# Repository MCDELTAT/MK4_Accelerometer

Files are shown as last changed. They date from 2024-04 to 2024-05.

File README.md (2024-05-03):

## Prusa MK4 Accelerometer

If you're reading this it's likely because you've [noticed][3] that your MK4 xBuddy Controller has a port reserved for an accelerometer and wondered "Hmmm. I wonder if that works."

I'm happy to report that the answer is "Yes." I found it to be reliable and working just fine, but in response to my demo, Josef Prusa himself responded "Hi! Please note the code is not tested on MK4 so you shouldn't count on it's results. There will be an official implementation but not ETA yet." Source [here][4].

This repository contains information, designs, and tools for using an accelerometer with the Prusa MK4 3D Printer.

This primary document is focused on being a quick start guide, while other documents in the repository contain more in-depth technical information about other aspects of the project.

## Future Work
Here's a roadmap of a few simple tasks that I'd like to accomplish with this project.

- [x] Design mounts for the Toolhead and Bed that work with both custom and off the shelf boards.
- [x] Test other chips like the LIS3DH for compatibility.
- [ ] Run print tests and document outcomes (IN PROGRESS)
- [ ] Design our own custom PCB with a compatible Molex Clik-MATE connector (IN PROGRESS-Design Complete, Validation Underway)
    * This will allow users to install an accelerometer quickly and without all the tools needed to solder.

## Compatability
* At the moment, only MCDELTAT has confirmed the accelerometer as working on firmware versions 5.2.1 and 6.0.0. Their printer uses the 2021 0.2.7 xBuddy board. Two other community members have tried on printers that use the 0.3.7 board and are not seeing similar signals on their ports. I'm working with them and hoping Prusa will release the older schematics so I can compare.

## ⚠️ HALT - Warranty Check
Q: Does this void my warranty?

A: Probably.

You can read the official Prusa Warranty on their website [here][1]. Quote "This warranty is **voided by:** ... Upgrades or add-ons that are not officially supported."

This modification does not require you to compile or upload any custom firmware to work. The release firmware directly from Prusa supports these boards, so this is purely a hardware addition. That said, I will include thorough warnings where appropriate to ensure that nothing goes wrong, should you follow the instructions correctly.

## Tools and Part Requirements
Here is a list of tools that will be needed to add an accelerometer board at the moment.
1. Clik-MATE 6 Pin Cable Assembly (MPN: 0151350606 for 600mm). Digikey [source][2]
2. LIS2DH Accelerometer board ready for SPI communication.
    * See the table below for a table of boards that have been tested and verified as working.
3. Soldering Iron and related tools.
4. (Optional) A multimeter will be helpful.
5. Mounts for the board. 3D Printable mounts for the X and Y-Axis can be found [here][9]. The mounts are designed for MK4 printers, but the mounting tray is designed to be modular. At the moment the only tray is for the generic accelerometer boards. I will provide another tray for my custom board later.
6. Some kind of computer capable of controlling your MK4 Printer and a USB-C Cable. I tested everything with a Raspberry Pi running Octoprint, but any compatible software should be functional. For example, Mainsail or Pronterface should be more than capable.

## Soldering Your Accelerometer Board
For this section, I will document the soldering procedure for the generic purple Chinese LIS2DH boards, as that is the first board I confirmed to be working.

1. Power off your printer. Unplug it from it's power source. 
2. (Optional but recommended). Insert one end of your cable assembly into the Accelerometer port of the board. The connector is keyed and will only fit one direction, with the release arm facing towards the center of the board (back of the printer). Pull it back out and use a marker to color the top side of the connector. This will help you to keep track of which pin belongs to each cable.
3. Cut the cable assembly with a wire stripper or other tool. Goodbye beautiful connector.
4. Strip off approximately 5mm of the outer wire insulator for each cable.
5. (Optional tinning technique). Heat up your soldering iron, twist the stranded wires of a single cable together tightly, and apply solder to the wires. This makes it into one solid connector and makes it easier to solder to the accelerometer board later.
6. Identify the first wire to solder. If you did step two, the top side that you marked is pin 6 on the Prusa Schematics and Connector documentation. (See the Diagram below). On the Digikey cable assembly, they use tape in the middle of the cables to group them to together. We have two options:

    a) Cut the tape and visually trace the cables.

    b) Leave the tape intact and use a multimeter to buzz out which cable is connected to each connector pin. This can be done by switching to continuity mode, touching one lead to a cable of your choice, and the other to small pad on the back of the connector.
7. Solder the wire to the correct position. Repeat steps 5 and 6, finding the correct wires and soldering them to the board. A table is provided below for reference.
8. Snip the extra wire that wasn't covered by the solder joint.

## Pinout
Here is a reference table for the Prusa Connector Pins and the breakout board. Prusa's documentation supporting this is found [here][5].

| Connector | Pin (Prusa) | Pin (Accel Board) | Type | Function | GPIO | Limitations  |
|---|---|---|---|---|---|---|
| J29 (ACCELEROMETER) | 1 | CS | open drain output | SPI2 CS  | PA10 | Max 3.3V/5mA |
| J29 (ACCELEROMETER) | 2 | SCL | input/output | SPI2 SCL | PB10 | Max 5V/5mA |
| J29 (ACCELEROMETER) | 3 | SDA | input/output | SPI2 SDI | PC3  | Max 5V/5mA |
| J29 (ACCELEROMETER) | 4 | SDO | input/output | SPI2 SDO | PC2  | Max 5V/5mA |
| J29 (ACCELEROMETER) | 5 | VCC | 3V3 | Power | x | Max 50mA |
| J29 (ACCELEROMETER) | 6 | GND | GND | Power | x | x |

## Pinout Images
### Connector Side:
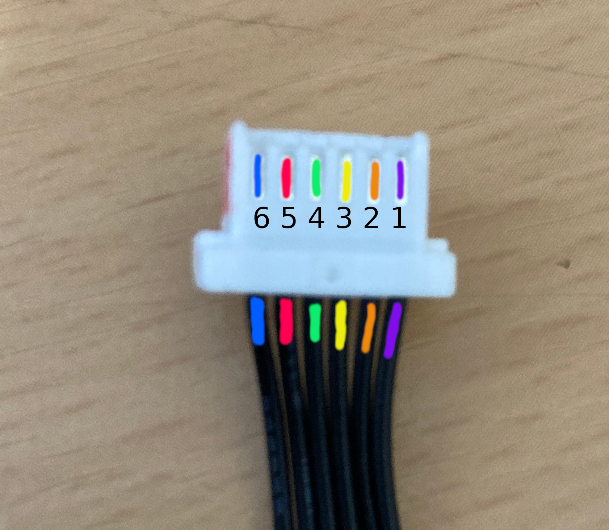
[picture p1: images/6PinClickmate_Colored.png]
ClickMate Male Connector Colored Pinout


### Adafruit Board:
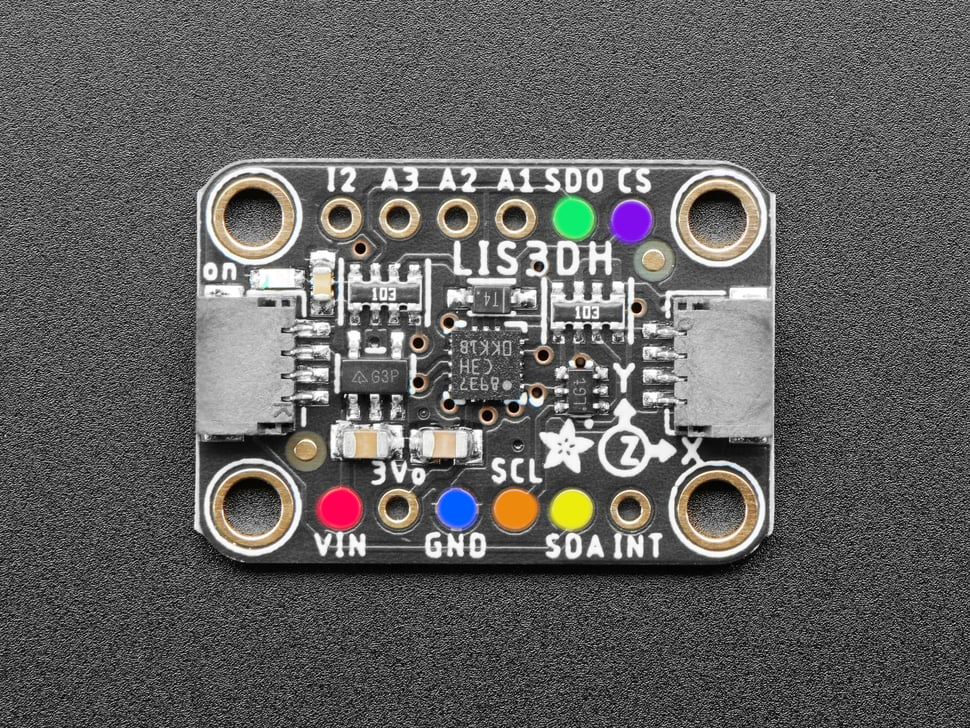
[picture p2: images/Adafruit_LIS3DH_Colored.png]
Adafruit LIS3DH Board Colored Pinout


### Generic LIS2DH Board:
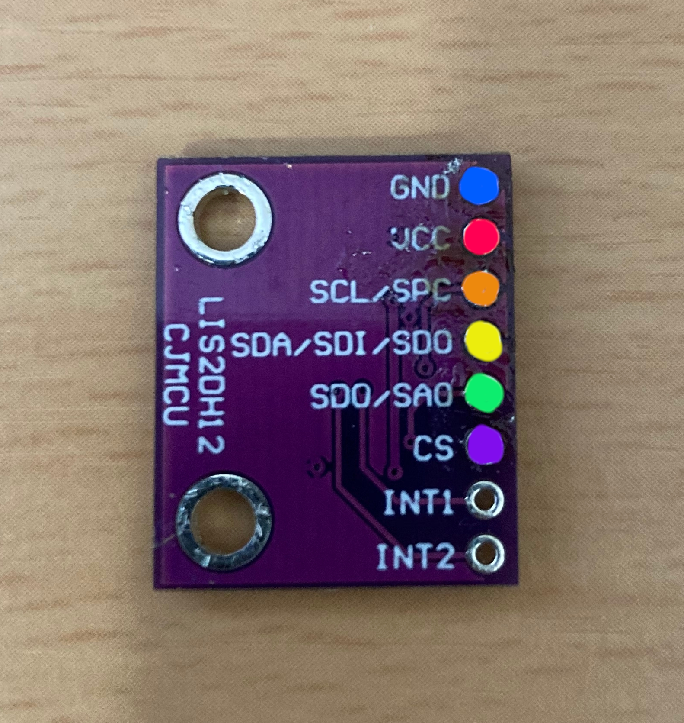
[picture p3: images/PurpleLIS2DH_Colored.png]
Generic LIS2DH Board Colored Pinout


## Compatible Boards:

| Board Name | Testing Status | Source | Notes |
|---|---|---|---|
| NOYITO LIS2DH12TR Development Board | WORKING | https://a.co/d/4UiPgB6 | This board is very generic and can be found many places ranging from $4 to $13. They likely all come from the same place. |
| Sparkfun SPX-15760 LIS2DH12 (Qwiic) | FAIL | https://www.sparkfun.com/products/retired/15760 | This board is hard wired for I2C, while the Prusa MK4 expects an SPI compatible device, so this will not work. |
| Adafruit LIS3DH Triple-Axis Accelerometer (Recommended) | WORKING | https://www.adafruit.com/product/2809 | The LIS3DH has a few more features we won't be using, however I confirmed it to work similarly. Since Adafruit has a solid supply chain, this is likely the best all around choice. Minor Con: The breakout board has pins on both sides, requiring cables to be on both sides, so it is a little messier.

## Using the Accelerometer
If you are hoping to get useful values out of the accelerometer, emphasize doing any pending maintenance first. Lube the smooth rods/bearings. Check for scratches. Check belt tension, etc. Each of these factors will change these results if you fix them later, so just do them now to avoid retesting. See Prusa's official docs for recommended regular maintenance [here][8].

1. Once you are confident your connections are going to the correct pins, plug the accelerometer into the MK4 Buddy board and the mounts.
2. Connect to the printer over USB-C to issue GCODE.
3. ⚠️ **IMPORTANT STEP** Before setting any parameters, gather the values that Prusa originally set on the printer. This will allow you to roll back to those values later if you want. In a GCODE control window, issue the `M593` command with no arguments. This will return the existing Input Shaping (IS) parameters. An example of my output can be found below. If you want to see all my Input Shaping testing results, see [Testing][6].
```
Send: M593
Recv: echo:axis X type=MZV freq=50.700001 damp=0.100000 vr=20.000000
Recv: echo:axis Y type=MZV freq=40.599998 damp=0.100000 vr=20.000000
Recv: echo:axis Z disabled
Recv: echo:weight_adjust y freq_delta=-20.000000 mass_limit=800.000000
Recv: ok
```
4. Issue the following command `M959 X F40.0 G60.0 N10`. This tests the X-Axis starting at 40Hz and ending at 60Hz, with a very quick sample size. The results this produces should not be used. It is provided here purely as a way to quickly test that you wired up the sensor correctly.
5. Now to test the X-Axis, you likely want to run the default workflow, which is over a large frequency range and sample size.
6. The command above gave us a general range, but now we can confirm a second time by running it over a smaller range with more samples. For example, if step 5 returned a frequency of 79.0Hz, then I can test from 65 to 85Hz, at steps of 0.5Hz, with 100 Samples. This can be done with the command `M959 X F65.0 G85.0 H0.5`. See below for a list of parameters to the M959 command.
7. Once you are satisfied with the results and think you have a consistent number, we will save the values. See the official documentation for the `M593` command [here][7]. Assuming I got the following results `Recv: ZV shaper selected Recv: Frequency: 79.00 damping ratio: 0.17444`

    a) To do this temporarily (until you shut off the printer), run the following command `M593 X D0.17444 F79.00 T0`. Note the lack of the `W` parameter, the parameter to save it to the EEPROM.

    b) To save it permanently, run the following command `M593 X D0.17444 F79.00 T0 W`.

## M959 Command
The `M959` command does all the heavy lifting in our testing. It's parameters are only listed in the source code, so I've copied them here for convenience.
```
/\*\*  
 \* u/brief Tune input shaper  
 \*  
 \* - X<direction> Vibrate with X motor, start in direction 1 or -1  
 \* - Y<direction> Vibrate with Y motor, start in direction 1 or -1  
 \* - Z<direction> Vibrate with Z motor, start in direction 1 or -1  
 \* - K           select Klipper tune algorithm  
 \* - KM          select Klipper Marek modified tune algorithm  
 \* - F<Hz>       Start frequency  
 \* - G<Hz>       End frequency  
 \* - H<Hz>       Frequency step  
 \* - A<mm/s-2>   Acceleration  
 \* - N<cycles>   Number of excitation signal periods  
 \*               of active measurement.  
 \*/  
```

[1]: https://help.prusa3d.com/article/warranty_2288
[2]: https://www.digikey.com/en/products/detail/molex/0151350606/6830172
[3]: https://help.prusa3d.com/article/accessory-connectors-mk4_622345
[4]: https://www.reddit.com/r/prusa3d/comments/1b5wych/comment/ktben9d/?utm_source=share&utm_medium=web2x&context=3
[5]: https://help.prusa3d.com/article/accessory-connectors-mk4_622345
[6]: ./Testing.md
[7]: https://help.prusa3d.com/article/buddy-firmware-specific-g-code-commands_633112#m-codes
[8]: https://help.prusa3d.com/article/regular-printer-maintenance-mk4_419000
[9]: https://www.printables.com/model/839201-mk4-accelerometer-mounts-for-x-and-y-axis-input-sh

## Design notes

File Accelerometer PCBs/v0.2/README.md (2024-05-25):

## Prusa MK4 Accelerometer v0.2

🛑 Status: Design complete, have ordered PCBs, have not tried on a real printer.

This board design fixes a large error made in the last revision, namely, the pinout is correct for a stock cable purchased from Digikey. Thus you should be able to buy cables from them, and immediately plug it into your printer. I also moved a silkscreen around the LIS2DH chip for hopefully better visual alignment. Finally, as reported in issue #1 of the repo, a 2.2K may be added to make this circuit compatible with 0.3.7 and 0.4.4 boards.

This is the bare minimum reference circuit as provided by STMicroelectronics, with an LED for reference.

BOM:
| Label | Digikey Part Num | Quantity | Description |
| ----- | --- | --- | --- |
| C1 | 1292-0201X104K250CT-ND | 1 | 0603 100nF Ceramic Capacitor |
| C2 | CL10A106MQ8NNNC | 1 | 0603 10uF Ceramic Capacitor |
| D1 | IN-S63AT5G | 1 | 0603 Green LED 525nm |
| R1 | RC0603FR-07120RL | 1 | 0603 120Ohm Resistor 1/10W |
| R2 | ERJ-H3GJ222V | 1 | 0603 2.2K Resistor Panasonic 1/8W  |
| J1 | 5025840670 | 1 | Molex Clickmate 6Pin SMT Connector |
| U1 | LIS2DHTR | 1 | LIS2DHTR MEMS Accelerometer |

When aligning the LIS2DHTR by hand, make sure the circle is in the top right corner, matching the stars near the LGA-12 pads.

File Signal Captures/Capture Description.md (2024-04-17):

## Experiment Setup
I used a premade cable assembly, tinned the stranded wire, and inserted that into my breadboard. I used my multimeter to buzz out the correct pins and cables, and inserted them in order Pins 1-6 from the MK4 Board. I then hooked up my Logic Analyzer to each of those pins, and it should have been numbered correctly. Pulseview and/or most Logic Analyzers are zero indexed, but just think of them in order. I.E. this was the pinout from board to LA.

| MK4 Board Pin | Logic Analyzer Pin |
| --- | --- |
| Pin 1 | D0 |
| Pin 2 | D1 |
| Pin 3 | D2 |
| Pin 4 | D3 |
| Pin 5 | D4 |
| Pin 6 | GND |

I've provided the raw capture files to look at if you have Pulseview or other similar software set up, or screenshots of what is basically the only important fields.

Image 1:
This shows the printers idle state, with the first changes happening when the M959 command is issued. The payload shown in image 2 is the grouping where D1-D4 are all active.

Image 2:
This shows the payload response, zoomed in from image 1. None of the channels are the same, which seems to indicate it is not a 3-Pin SPI setup. I currently have MK4 Pin 4 (D3 here) disconnected because I'm not sure where it can be wired to on the board. The only remaining pins are INT1 and INT2 on the Sparkfun Breakout Board.

Image 3:
This is zoomed out to show that D1 is the SCL pin because it's the only one with regularly occuring writes.

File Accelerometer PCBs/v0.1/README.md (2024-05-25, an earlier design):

## Prusa MK4 Accelerometer v0.1

🛑 This board was submitted for reference, but it won't work without a custom cable. This is because I got the pins backwards on the Click-mate connector because I had crimped my own. When trying with a stock cable from Digikey, I noticed the error. This will be fixed in the next revision. In other words: don't try to make this one.

This is the bare minimum reference circuit as provided by STMicroelectronics, with an LED for reference.

BOM:
| Digikey Part Num | Quantity | Description |
| --- | --- | --- |
| 1292-0201X104K250CT-ND | 1 | 0603 100nF Ceramic Capacitor |
| CL10A106MQ8NNNC | 1 | 0603 10uF Ceramic Capacitor |
| IN-S63AT5G | 1 | 0603 Green LED 525nm |
| RC0603FR-07120RL | 1 | 0603 120Ohm Resistor 1/10W |
| 5025840670 | 1 | Molex Clickmate 6Pin SMT Connector |
| LIS2DHTR | 1 | LIS2DHTR MEMS Accelerometer |

When aligning the LIS2DHTR by hand, make sure the circle is in the top right corner, matching the stars near the LGA-12 pads.

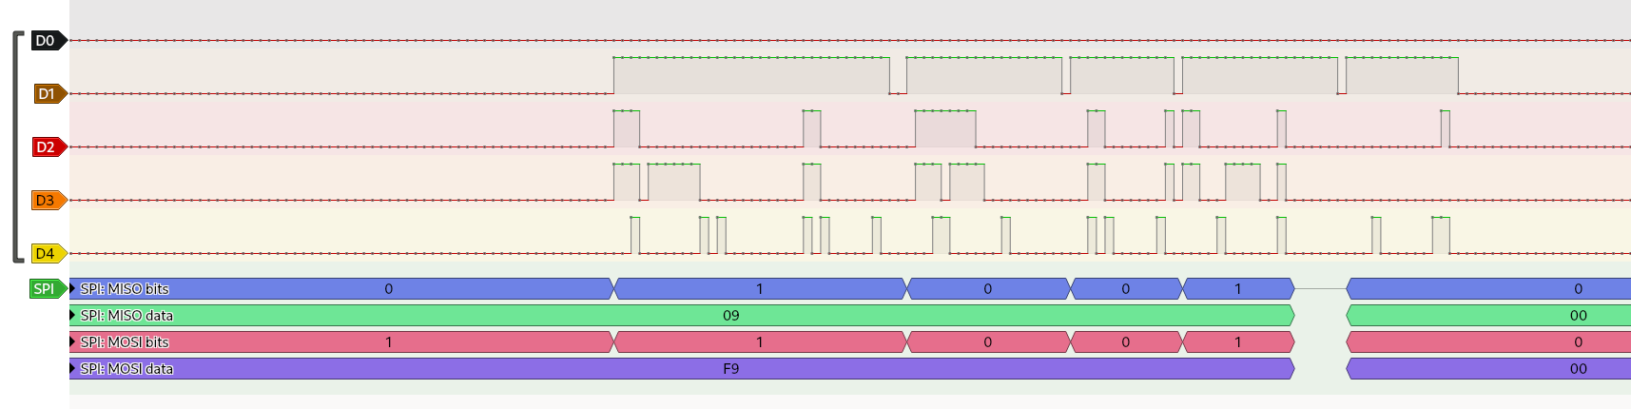
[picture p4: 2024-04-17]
Signal Captures/2_M959 Payload_2MHz.png

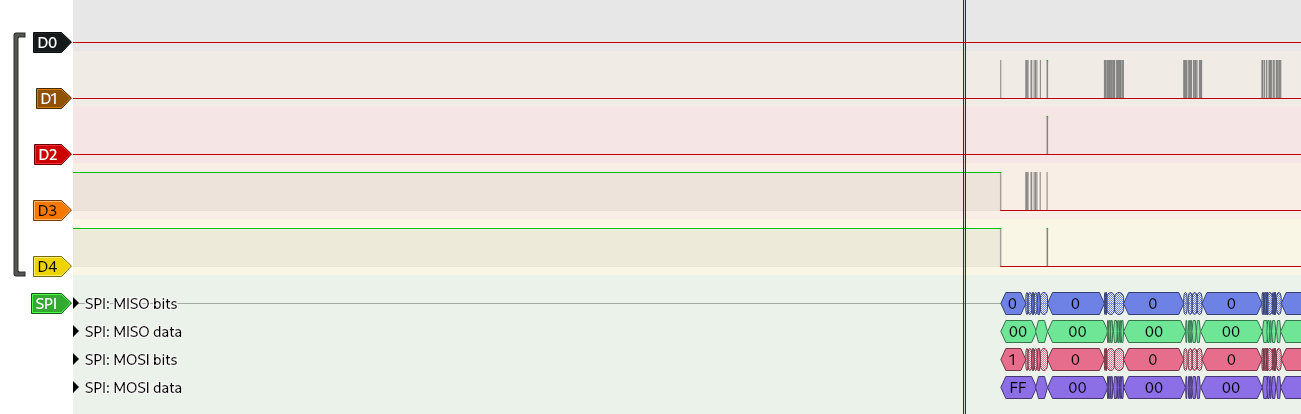
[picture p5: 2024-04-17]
Signal Captures/3_ZoomedOutSCL_2MHz.png

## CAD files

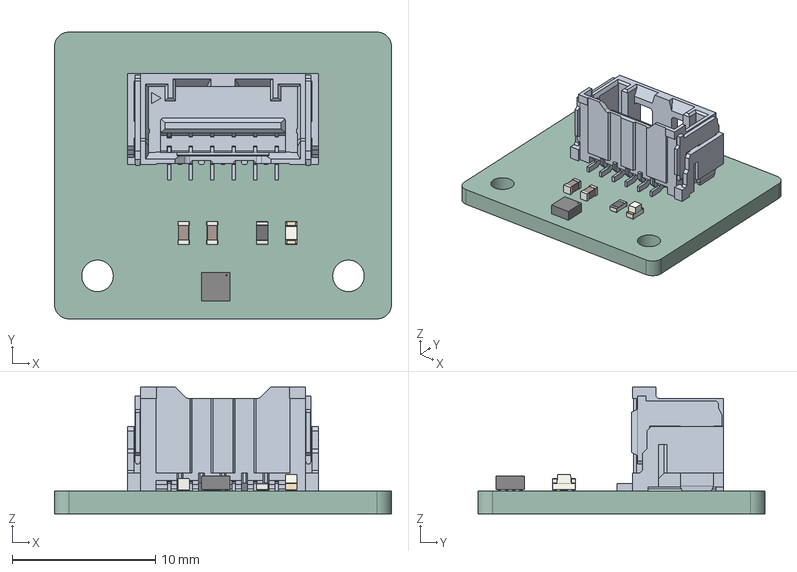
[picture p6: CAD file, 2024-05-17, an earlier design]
Accelerometer PCBs/v0.1/MK4 Accelerometer.step
23.5 x 20.0 x 8.83 mm
C_0603_1608Metric x 2
R_0603_1608Metric
LED_0603_1608Metric
MK4 Accelerometer_PCB

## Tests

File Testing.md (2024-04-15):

# M593 Command
* These are the values that Prusa ships with the MK4 from the factory.

```
Send: M593
Recv: echo:axis X type=MZV freq=50.700001 damp=0.100000 vr=20.000000
Recv: echo:axis Y type=MZV freq=40.599998 damp=0.100000 vr=20.000000
Recv: echo:axis Z disabled
Recv: echo:weight_adjust y freq_delta=-20.000000 mass_limit=800.000000
Recv: ok
```

# M959 X
* These are the X-AXIS values after the very first run on the accelerometer mounted with tape, filament rolls on top.

<details>
  <summary>Click to expand results.</summary>
  
  ### Results
  
  ```
  Send: M959
  Recv:  T:25.00/0.00 B:23.54/0.00 X:24.39/36.00 A:32.65/0.00 @:0 B@:0 HBR@:0
  Recv: echo:busy: processing
  Printer seems to support the busy protocol, will adjust timeouts and set busy interval accordingly
  Recv:  T:25.00/0.00 B:23.66/0.00 X:24.38/36.00 A:32.67/0.00 @:0 B@:0 HBR@:0
  Recv: echo:busy: processing
  Recv:  T:25.00/0.00 B:23.54/0.00 X:24.44/36.00 A:32.94/0.00 @:0 B@:0 HBR@:0
  Recv: echo:busy: processing
  Recv:  T:25.00/0.00 B:23.57/0.00 X:24.52/36.00 A:32.81/0.00 @:0 B@:0 HBR@:0
  Recv: echo:busy: processing
  Recv:  T:25.00/0.00 B:23.45/0.00 X:24.53/36.00 A:32.90/0.00 @:0 B@:0 HBR@:0
  Recv: echo:busy: processing
  Recv:  T:25.00/0.00 B:23.66/0.00 X:24.31/36.00 A:32.85/0.00 @:0 B@:0 HBR@:0
  Recv: echo:busy: processing
  Recv:  T:25.00/0.00 B:23.57/0.00 X:24.42/36.00 A:32.85/0.00 @:0 B@:0 HBR@:0
  Recv: echo:busy: processing
  Recv:  T:25.00/0.00 B:23.51/0.00 X:24.42/36.00 A:32.85/0.00 @:0 B@:0 HBR@:0
  Recv: Sample freq: 1271.70
  Recv: frequency[Hz] excitation[m/s^2] X[m/s^2] Y[m/s^2] Z[m/s^2] X_gain Y_gain Z_gain
  Recv: 5.00 2.50 0.00001 0.00001 0.00001 0.00000 0.00000 0.00000
  Recv: 6.00 2.50 2.56981 0.04276 0.04994 1.02773 0.01710 0.01997
  Recv: 7.00 2.50 2.71594 0.04854 0.05557 1.08626 0.01941 0.02223
  Recv: 8.00 2.50 2.51433 0.12741 0.05116 1.00519 0.05094 0.02045
  Recv: 9.00 2.50 2.65551 0.01630 0.03994 1.06210 0.00652 0.01597
  Recv: 10.00 2.50 2.66237 0.17689 0.05735 1.06412 0.07070 0.02292
  Recv: 11.00 2.50 3.37715 0.13786 0.09830 1.34983 0.05510 0.03929
  Recv: 12.00 2.50 1.76003 0.13427 0.03719 0.70363 0.05368 0.01487
  Recv: 13.00 2.50 2.01126 0.24073 0.07584 0.80388 0.09622 0.03031
  Recv: 14.00 2.50 2.17129 0.21547 0.06382 0.86842 0.08618 0.02553
  Recv: 15.00 2.50 2.26631 0.05034 0.06110 0.90515 0.02011 0.02440
  Recv: 16.00 2.50 2.37140 0.05349 0.06181 0.94805 0.02138 0.02471
  Recv: 17.00 2.50 2.43224 0.05484 0.06140 0.97176 0.02191 0.02453
  Recv: 18.00 2.50 2.49784 0.05424 0.05904 0.99824 0.02168 0.02360
  Recv: 19.00 2.50 2.54890 0.04812 0.06247 1.01836 0.01923 0.02496
  Recv: 20.00 2.51 2.63437 0.04283 0.07585 1.05085 0.01709 0.03026
  Recv: 21.00 2.50 2.66027 0.06906 0.07869 1.06296 0.02759 0.03144
  Recv: 22.00 2.51 2.67724 0.11700 0.05219 1.06754 0.04665 0.02081
  Recv: 23.00 2.51 2.76816 0.22427 0.06783 1.10457 0.08949 0.02707
  Recv: 24.00 2.50 2.90828 0.31917 0.12075 1.16268 0.12760 0.04827
  Recv: 25.00 2.51 2.93145 0.63307 0.14050 1.16620 0.25185 0.05590
  Recv: 26.00 2.50 2.82576 0.73563 0.15303 1.12943 0.29403 0.06116
  Recv: 27.00 2.50 2.91871 0.75405 0.17920 1.16737 0.30159 0.07167
  Recv: 28.00 2.51 3.10222 0.76670 0.21476 1.23360 0.30488 0.08540
  Recv: 29.00 2.51 3.25590 0.80222 0.24970 1.29673 0.31950 0.09945
  Recv: 30.00 2.51 3.45424 0.92005 0.30906 1.37655 0.36665 0.12316
  Recv: 31.00 2.51 3.72310 1.30650 0.41474 1.48127 0.51980 0.16501
  Recv: 32.00 2.50 4.07973 1.34880 0.31766 1.63101 0.53923 0.12700
  Recv: 33.00 2.53 4.56324 1.02644 0.18510 1.80667 0.40639 0.07328
  Recv: 34.00 2.51 5.09204 1.03784 0.29049 2.02867 0.41347 0.11573
  Recv: 35.00 2.51 4.25541 0.97996 0.36270 1.69624 0.39062 0.14458
  Recv: 36.00 2.53 3.86179 1.24246 0.46692 1.52868 0.49182 0.18483
  Recv: 37.00 2.53 3.34636 1.77222 0.55860 1.32089 0.69954 0.22049
  Recv: 38.00 2.53 2.51011 1.40633 0.63854 0.99226 0.55593 0.25242
  Recv: 39.00 2.51 1.99907 0.90557 0.59862 0.79503 0.36014 0.23807
  Recv: 40.00 2.53 1.97812 0.64066 0.58098 0.78291 0.25357 0.22994
  Recv: 41.00 2.53 2.25060 0.61650 0.64418 0.88953 0.24367 0.25460
  Recv: 42.00 2.52 2.53151 0.84608 0.71904 1.00280 0.33516 0.28483
  Recv: 43.00 2.51 2.77919 1.56955 0.88612 1.10759 0.62551 0.35314
  Recv: 44.00 2.53 2.55647 1.95948 0.83477 1.00976 0.77396 0.32972
  Recv: 45.00 2.55 2.46971 1.41689 0.60745 0.96920 0.55603 0.23838
  Recv: 46.00 2.51 2.44157 1.06187 0.44924 0.97425 0.42371 0.17926
  Recv: 47.00 2.51 2.76456 1.04807 0.35715 1.10264 0.41802 0.14245
  Recv: 48.00 2.50 3.00827 1.09309 0.29118 1.20266 0.43700 0.11641
  Recv: 49.00 2.55 3.34330 0.96786 0.11447 1.31243 0.37994 0.04494
  Recv: 50.00 2.53 3.86306 0.65615 0.10041 1.52745 0.25944 0.03970
  Recv: 51.00 2.50 4.31194 0.47428 0.11172 1.72277 0.18949 0.04464
  Recv: 52.00 2.54 4.81304 0.35864 0.15025 1.89841 0.14146 0.05926
  Recv: 53.00 2.56 4.89690 0.21984 0.23166 1.90954 0.08573 0.09034
  Recv: 54.00 2.52 4.95059 0.46405 0.30916 1.96590 0.18427 0.12277
  Recv: 55.00 2.54 5.26667 0.64007 0.35082 2.07535 0.25222 0.13824
  Recv: 56.00 2.55 5.16161 1.17550 0.56014 2.02142 0.46036 0.21936
  Recv: 57.00 2.57 4.05413 1.44395 0.68691 1.58037 0.56288 0.26777
  Recv: 58.00 2.57 3.49556 1.37256 0.65368 1.35850 0.53342 0.25404
  Recv: 59.00 2.58 3.44746 1.44474 0.57429 1.33793 0.56069 0.22288
  Recv: 60.00 2.58 3.41804 1.26882 0.73130 1.32690 0.49256 0.28389
  Recv: 61.00 2.57 3.10049 0.82092 0.81595 1.20607 0.31933 0.31740
  Recv: 62.00 2.56 3.52276 0.58458 1.15116 1.37561 0.22827 0.44952
  Recv: 63.00 2.55 3.36280 0.96611 1.07050 1.32071 0.37943 0.42043
  Recv: 64.00 2.53 3.16548 1.32171 0.83876 1.25285 0.52311 0.33197
  Recv: 65.00 2.50 3.28268 1.62184 0.75523 1.31205 0.64823 0.30186
  Recv: 66.00 2.58 4.20413 2.07211 0.87979 1.62981 0.80329 0.34107
  Recv: 67.00 2.55 5.22470 2.45304 1.05983 2.05090 0.96291 0.41602
  Recv: 68.00 2.51 5.19729 2.23599 0.94721 2.07060 0.89082 0.37737
  Recv: 69.00 2.58 5.12747 1.63637 0.60033 1.98400 0.63317 0.23229
  Recv: 70.00 2.54 4.91714 1.30907 0.31068 1.93668 0.51560 0.12237
  Recv: 71.00 2.61 5.34875 1.34975 0.23810 2.04775 0.51675 0.09115
  Recv: 72.00 2.56 5.26150 1.42889 0.30294 2.05672 0.55855 0.11842
  Recv: 73.00 2.63 4.29416 1.37820 0.37021 1.63291 0.52408 0.14078
  Recv: 74.00 2.57 3.39127 1.29120 0.46525 1.32101 0.50296 0.18123
  Recv: 75.00 2.64 2.59065 1.16777 0.65340 0.98241 0.44283 0.24778
  Recv: 76.00 2.57 1.98945 1.01574 0.91051 0.77552 0.39595 0.35493
  Recv: 77.00 2.63 2.04336 0.88589 1.29772 0.77598 0.33642 0.49282
  Recv: 78.00 2.55 2.11097 1.06643 1.76642 0.82719 0.41788 0.69217
  Recv: 79.00 2.62 2.17775 1.16523 2.20661 0.83189 0.44511 0.84291
  Recv: 80.00 2.53 1.75430 1.03352 1.92596 0.69433 0.40905 0.76227
  Recv: 81.00 2.59 1.51874 1.08997 1.88587 0.58634 0.42081 0.72808
  Recv: 82.00 2.65 1.29722 1.22946 1.84218 0.48868 0.46315 0.69397
  Recv: 83.00 2.55 1.21621 1.30503 1.63035 0.47700 0.51184 0.63943
  Recv: 84.00 2.61 1.75229 1.42654 1.42527 0.67099 0.54626 0.54577
  Recv: 85.00 2.67 2.78250 1.53803 1.22157 1.04056 0.57517 0.45683
  Recv: 86.00 2.55 3.41133 1.49909 0.93839 1.33524 0.58676 0.36730
  Recv: 87.00 2.61 4.61156 1.84963 1.13152 1.76377 0.70742 0.43277
  Recv: 88.00 2.68 5.62353 2.19797 1.57298 2.10221 0.82165 0.58802
  Recv: 89.00 2.54 6.17903 2.82836 2.03770 2.43196 1.11319 0.80201
  Recv: 90.00 2.60 9.55151 3.69564 2.18241 3.67624 1.42240 0.83998
  Recv: 91.00 2.66 13.52402 4.73311 2.45529 5.09143 1.78189 0.92435
  Recv: 92.00 2.51 13.58129 4.57458 2.19200 5.41931 1.82539 0.87467
  Recv: 93.00 2.56 12.51249 4.13065 1.87603 4.88604 1.61299 0.73258
  Recv: 94.00 2.62 11.23692 3.68820 1.67911 4.29507 1.40974 0.64180
  Recv: 95.00 2.67 9.42394 3.10554 1.40332 3.52667 1.16217 0.52516
  Recv: 96.00 2.50 8.08461 2.69507 1.27876 3.23209 1.07744 0.51123
  Recv: 97.00 2.55 5.80664 2.00541 1.03327 2.27378 0.78528 0.40461
  Recv: 98.00 2.61 6.40697 2.33591 1.29339 2.45792 0.89613 0.49619
  Recv: 99.00 2.66 5.83607 2.29425 1.42093 2.19390 0.86246 0.53416
  Recv: 100.00 2.71 5.45344 2.36556 1.63537 2.00927 0.87157 0.60254
  Recv: 101.00 2.52 4.20339 2.06698 1.64012 1.67000 0.82121 0.65162
  Recv: 102.00 2.57 3.91027 2.20347 1.95271 1.52323 0.85835 0.76067
  Recv: 103.00 2.62 3.22694 2.15298 2.15342 1.23275 0.82248 0.82265
  Recv: 104.00 2.67 3.27613 2.51767 2.84733 1.22759 0.94339 1.06692
  Recv: 105.00 2.72 3.24477 2.57464 3.30659 1.19279 0.94645 1.21552
  Recv: 106.00 2.77 3.15214 2.24790 3.37561 1.13698 0.81082 1.21759
  Recv: 107.00 2.54 3.23083 1.71721 2.94681 1.27076 0.67542 1.15905
  Recv: 108.00 2.59 3.16095 1.24392 2.40903 1.22036 0.48025 0.93006
  Recv: 109.00 2.64 3.17708 0.96030 2.08313 1.20418 0.36397 0.78955
  Recv: 110.00 2.69 3.04920 0.73224 1.77430 1.13480 0.27251 0.66033
  Recv: 111.00 2.74 2.93966 0.57429 1.60053 1.07441 0.20990 0.58497
  Recv: 112.00 2.79 2.84359 0.42291 1.42980 1.02082 0.15182 0.51328
  Recv: 113.00 2.52 2.43028 0.28224 1.17159 0.96421 0.11198 0.46482
  Recv: 114.00 2.57 2.28961 0.21093 1.05734 0.89253 0.08222 0.41217
  Recv: 115.00 2.61 2.37333 0.18274 1.04894 0.90914 0.07000 0.40181
  Recv: 116.00 2.66 2.44358 0.16076 1.09611 0.91998 0.06053 0.41268
  Recv: 117.00 2.70 2.41911 0.08795 1.02759 0.89527 0.03255 0.38029
  Recv: 118.00 2.75 2.49760 0.09708 0.94517 0.90872 0.03532 0.34389
  Recv: 119.00 2.80 2.50041 0.26954 0.82365 0.89452 0.09643 0.29466
  Recv: 120.00 2.84 2.51852 0.21075 0.90610 0.88604 0.07414 0.31878
  Recv: 121.00 2.53 1.91509 0.14600 0.68662 0.75732 0.05774 0.27152
  Recv: 122.00 2.57 2.27718 0.16564 0.86457 0.88581 0.06443 0.33631
  Recv: 123.00 2.61 2.12363 0.17292 0.81424 0.81270 0.06618 0.31161
  Recv: 124.00 2.66 2.17150 0.23844 0.78829 0.81767 0.08978 0.29683
  Recv: 125.00 2.70 2.14251 0.27571 0.78416 0.79390 0.10216 0.29057
  Recv: 126.00 2.74 2.07725 0.28448 0.80108 0.75755 0.10375 0.29214
  Recv: 127.00 2.79 2.09033 0.28852 0.90715 0.75036 0.10357 0.32564
  Recv: 128.00 2.83 2.09107 0.28090 0.95646 0.73894 0.09927 0.33799
  Recv: 129.00 2.87 2.18036 0.28082 1.05612 0.75859 0.09770 0.36745
  Recv: 130.00 2.50 1.87618 0.23185 0.99334 0.74989 0.09267 0.39703
  Recv: 131.00 2.54 1.95238 0.22039 1.13257 0.76848 0.08675 0.44579
  Recv: 132.00 2.58 1.98736 0.21855 1.23330 0.77044 0.08473 0.47811
  Recv: 133.00 2.62 1.72903 0.20792 1.08764 0.66025 0.07940 0.41533
  Recv: 134.00 2.66 2.04372 0.25933 1.33451 0.76881 0.09755 0.50202
  Recv: 135.00 2.70 2.06743 0.29877 1.34216 0.76625 0.11073 0.49745
  Recv: 136.00 2.74 2.08275 0.31641 1.32777 0.76062 0.11555 0.48490
  Recv: 137.00 2.78 2.11923 0.33880 1.40565 0.76269 0.12193 0.50588
  Recv: 138.00 2.82 2.14369 0.33782 1.47204 0.76035 0.11982 0.52212
  Recv: 139.00 2.86 1.98459 0.31086 1.37742 0.69383 0.10868 0.48155
  Recv: 140.00 2.90 2.06839 0.33170 1.48942 0.71283 0.11431 0.51330
  Recv: 141.00 2.94 2.03558 0.33551 1.46952 0.69161 0.11399 0.49928
  Recv: 142.00 2.99 1.95598 0.33816 1.47059 0.65523 0.11328 0.49263
  Recv: 143.00 2.52 1.57571 0.26074 1.17880 0.62459 0.10335 0.46726
  Recv: 144.00 2.56 1.41965 0.25286 1.09467 0.55494 0.09884 0.42791
  Recv: 145.00 2.59 1.48163 0.27620 1.22381 0.57121 0.10648 0.47181
  Recv: 146.00 2.63 1.47685 0.28365 1.27637 0.56159 0.10786 0.48536
  Recv: 147.00 2.67 1.41150 0.27967 1.25226 0.52946 0.10491 0.46973
  Recv: 148.00 2.70 1.31268 0.28802 1.17215 0.48577 0.10658 0.43376
  Recv: 149.00 2.74 1.13737 0.27113 0.99769 0.41526 0.09899 0.36426
  Recv: 150.00 2.78 1.28481 0.33007 1.13784 0.46286 0.11891 0.40991
  Recv: Maximum resonant gain: 5.42 at frequency: 92.00
  Recv: ZV shaper selected
  Recv: Frequency: 92.00 damping ratio: 0.11728
  Recv:  T:25.00/0.00 B:23.63/0.00 X:25.75/36.00 A:35.31/0.00 @:0 B@:0 HBR@:0
  Recv: ok
  Send: M113 S2
  Recv: ok
  Recv:  T:25.00/0.00 B:23.60/0.00 X:25.75/36.00 A:35.29/0.00 @:0 B@:0 HBR@:0
  Recv:  T:25.00/0.00 B:23.51/0.00 X:25.84/36.00 A:35.35/0.00 @:0 B@:0 HBR@:0
  ```
</details>

# M959 X with Mount
* Thanks to a fellow redditor, we already have a mount for the Chinese PCBs. I tested it out and got the following values. Note that it is fairly different result from the one with it taped on.

<details>
  <summary>Click to expand results.</summary>
  
  ### Results  
  
  ```
  Send: M959
  Recv: Sample freq: 1271.62
  Recv: frequency[Hz] excitation[m/s^2] X[m/s^2] Y[m/s^2] Z[m/s^2] X_gain Y_gain Z_gain
  Recv: 5.00 2.50 0.00000 0.00000 0.00000 0.00000 0.00000 0.00000
  Recv: 6.00 2.50 2.55800 0.02148 0.07608 1.02301 0.00859 0.03043
  Recv: 7.00 2.50 2.50135 0.03046 0.06315 1.00043 0.01218 0.02526
  Recv: 8.00 2.50 2.57716 0.06620 0.08518 1.03031 0.02646 0.03405
  Recv: 9.00 2.50 2.63526 0.03700 0.07325 1.05399 0.01480 0.02930
  Recv: 10.00 2.50 2.77347 0.03446 0.08108 1.10853 0.01377 0.03241
  Recv: 11.00 2.50 3.21814 0.11511 0.11625 1.28628 0.04601 0.04646
  Recv: 12.00 2.50 1.94496 0.18943 0.05725 0.77756 0.07573 0.02289
  Recv: 13.00 2.50 2.08049 0.32533 0.01295 0.83155 0.13003 0.00518
  Recv: 14.00 2.50 2.14194 0.12650 0.01050 0.85668 0.05059 0.00420
  Recv: 15.00 2.50 2.31853 0.06694 0.01306 0.92601 0.02673 0.00522
  Recv: 16.00 2.50 2.37435 0.04770 0.01008 0.94923 0.01907 0.00403
  Recv: 17.00 2.50 2.47263 0.04247 0.01154 0.98790 0.01697 0.00461
  Recv: 18.00 2.50 2.48556 0.04343 0.01218 0.99333 0.01736 0.00487
  Recv: 19.00 2.50 2.58163 0.05071 0.01108 1.03143 0.02026 0.00443
  Recv: 20.00 2.51 2.72121 0.06174 0.03867 1.08550 0.02463 0.01543
  Recv: 21.00 2.50 2.45853 0.04704 0.08491 0.98235 0.01879 0.03393
  Recv: 22.00 2.51 2.52754 0.01477 0.05852 1.00785 0.00589 0.02333
  Recv: 23.00 2.51 2.62988 0.00481 0.03687 1.04939 0.00192 0.01471
  Recv: 24.00 2.50 2.50517 0.01418 0.03296 1.00153 0.00567 0.01318
  Recv: 25.00 2.51 2.86479 0.04407 0.10297 1.13969 0.01753 0.04096
  Recv: 26.00 2.50 2.89823 0.06899 0.21070 1.15839 0.02757 0.08422
  Recv: 27.00 2.50 2.93730 0.08696 0.33009 1.17481 0.03478 0.13202
  Recv: 28.00 2.51 3.03705 0.10892 0.43036 1.20768 0.04331 0.17113
  Recv: 29.00 2.51 3.06286 0.11801 0.45124 1.21985 0.04700 0.17972
  Recv: 30.00 2.51 3.19471 0.17271 0.57342 1.27312 0.06882 0.22851
  Recv: 31.00 2.51 3.32233 0.27986 0.85323 1.32182 0.11135 0.33947
  Recv: 32.00 2.50 3.43869 0.51912 1.37633 1.37473 0.20753 0.55023
  Recv: 33.00 2.53 3.56397 0.46089 1.05748 1.41104 0.18247 0.41867
  Recv: 34.00 2.51 3.86270 0.44472 0.86679 1.53890 0.17718 0.34533
  Recv: 35.00 2.51 4.14800 0.67732 1.10004 1.65342 0.26999 0.43848
  Recv: 36.00 2.53 3.98462 0.77147 0.57799 1.57730 0.30539 0.22880
  Recv: 37.00 2.53 3.66720 0.60179 0.59985 1.44754 0.23754 0.23678
  Recv: 38.00 2.53 3.27544 0.54746 0.71129 1.29481 0.21641 0.28118
  Recv: 39.00 2.51 3.04320 0.44717 0.79148 1.21028 0.17784 0.31477
  Recv: 40.00 2.53 3.09563 0.36883 0.85823 1.22521 0.14598 0.33967
  Recv: 41.00 2.53 3.44443 0.14554 0.89732 1.36138 0.05752 0.35466
  Recv: 42.00 2.52 3.86799 0.13351 1.22649 1.53221 0.05289 0.48584
  Recv: 43.00 2.51 4.06347 0.17500 1.62089 1.61941 0.06974 0.64597
  Recv: 44.00 2.53 3.87988 0.25627 2.00393 1.53249 0.10122 0.79152
  Recv: 45.00 2.55 4.92771 0.47841 3.07318 1.93379 0.18774 1.20601
  Recv: 46.00 2.51 4.88048 0.57929 3.53252 1.94745 0.23115 1.40958
  Recv: 47.00 2.51 4.05537 0.47162 2.87427 1.61748 0.18810 1.14640
  Recv: 48.00 2.50 3.42404 0.28073 1.64030 1.36888 0.11223 0.65577
  Recv: 49.00 2.55 3.90644 0.20922 0.90984 1.53349 0.08213 0.35716
  Recv: 50.00 2.53 3.84778 0.22316 0.88327 1.52141 0.08824 0.34924
  Recv: 51.00 2.50 4.42135 0.13961 0.59141 1.76649 0.05578 0.23629
  Recv: 52.00 2.54 5.16406 0.22954 0.44920 2.03686 0.09054 0.17718
  Recv: 53.00 2.56 5.27485 0.43225 1.58911 2.05692 0.16855 0.61967
  Recv: 54.00 2.52 4.36626 0.45961 1.85316 1.73386 0.18251 0.73590
  Recv: 55.00 2.54 3.95458 0.46529 1.71470 1.55832 0.18335 0.67568
  Recv: 56.00 2.55 3.67190 0.49579 1.54645 1.43801 0.19416 0.60563
  Recv: 57.00 2.57 3.74176 0.58155 1.54497 1.45860 0.22670 0.60226
  Recv: 58.00 2.57 3.96294 0.71058 1.49143 1.54014 0.27615 0.57962
  Recv: 59.00 2.58 4.48683 1.03433 1.67441 1.74130 0.40142 0.64983
  Recv: 60.00 2.58 4.62009 1.62849 2.35637 1.79354 0.63219 0.91475
  Recv: 61.00 2.57 4.11776 2.26446 3.36799 1.60178 0.88086 1.31013
  Recv: 62.00 2.56 3.61903 2.43280 3.78810 1.41320 0.94999 1.47922
  Recv: 63.00 2.55 3.55488 2.10652 3.26192 1.39614 0.82732 1.28109
  Recv: 64.00 2.53 3.96533 2.11171 3.24846 1.56942 0.83578 1.28570
  Recv: 65.00 2.50 4.17759 2.10669 3.27159 1.66974 0.84202 1.30762
  Recv: 66.00 2.58 3.39911 1.58371 2.52654 1.31773 0.61396 0.97946
  Recv: 67.00 2.55 2.09509 0.95325 1.60059 0.82240 0.37419 0.62829
  Recv: 68.00 2.51 2.19427 1.00848 1.69261 0.87420 0.40178 0.67434
  Recv: 69.00 2.58 2.72310 1.20203 1.90226 1.05366 0.46511 0.73605
  Recv: 70.00 2.54 2.83467 1.03812 1.57345 1.11647 0.40888 0.61972
  Recv: 71.00 2.61 2.92361 0.88563 1.41292 1.11929 0.33906 0.54093
  Recv: 72.00 2.56 2.89802 0.75233 1.28645 1.13284 0.29409 0.50287
  Recv: 73.00 2.63 2.47064 0.54292 1.05668 0.93949 0.20645 0.40182
  Recv: 74.00 2.57 2.31859 0.39666 0.96827 0.90316 0.15451 0.37717
  Recv: 75.00 2.64 3.10040 0.43149 1.25283 1.17571 0.16363 0.47509
  Recv: 76.00 2.57 4.25896 0.50080 1.49755 1.66022 0.19522 0.58377
  Recv: 77.00 2.63 6.75461 1.07130 2.27344 2.56511 0.40683 0.86336
  Recv: 78.00 2.55 8.67519 2.01622 3.19033 3.39939 0.79006 1.25014
  Recv: 79.00 2.62 10.45700 2.18530 3.36118 3.99452 0.83477 1.28395
  Recv: 80.00 2.53 9.49054 1.93664 3.10473 3.75622 0.76649 1.22881
  Recv: 81.00 2.59 8.22837 1.78570 2.76550 3.17676 0.68941 1.06769
  Recv: 82.00 2.65 7.26986 1.65718 2.37600 2.73866 0.62428 0.89508
  Recv: 83.00 2.55 5.99105 1.43168 1.88206 2.34972 0.56151 0.73815
  Recv: 84.00 2.61 5.12306 1.12174 1.48080 1.96173 0.42954 0.56703
  Recv: 85.00 2.67 4.63350 0.90918 1.17968 1.73277 0.34000 0.44116
  Recv: 86.00 2.55 3.86638 1.00874 1.20541 1.51335 0.39483 0.47181
  Recv: 87.00 2.61 3.28557 0.96325 1.17730 1.25662 0.36841 0.45028
  Recv: 88.00 2.68 3.10491 0.91408 1.16733 1.16069 0.34171 0.43637
  Recv: 89.00 2.54 2.49550 0.72651 0.99538 0.98219 0.28594 0.39176
  Recv: 90.00 2.60 2.14219 0.60774 0.92600 0.82450 0.23391 0.35640
  Recv: 91.00 2.66 1.72105 0.51028 0.85528 0.64793 0.19211 0.32199
  Recv: 92.00 2.51 1.26757 0.59748 0.68916 0.50580 0.23841 0.27499
  Recv: 93.00 2.56 1.22164 0.78625 0.56622 0.47704 0.30702 0.22110
  Recv: 94.00 2.62 1.29140 0.89445 0.54866 0.49361 0.34189 0.20971
  Recv: 95.00 2.67 1.31191 0.90066 0.54513 0.49095 0.33705 0.20400
  Recv: 96.00 2.50 1.17313 0.76656 0.47182 0.46900 0.30646 0.18863
  Recv: 97.00 2.55 1.40743 0.81932 0.49829 0.55112 0.32083 0.19512
  Recv: 98.00 2.61 1.49402 0.77644 0.45261 0.57316 0.29787 0.17364
  Recv: 99.00 2.66 1.51565 0.73059 0.45963 0.56976 0.27465 0.17278
  Recv: 100.00 2.71 1.48316 0.70133 0.47530 0.54646 0.25840 0.17512
  Recv: 101.00 2.52 1.17210 0.47756 0.35779 0.46567 0.18974 0.14215
  Recv: 102.00 2.57 1.45267 0.49955 0.49610 0.56588 0.19460 0.19325
  Recv: 103.00 2.62 1.35965 0.56003 0.49282 0.51941 0.21394 0.18827
  Recv: 104.00 2.67 1.34569 0.56731 0.47610 0.50424 0.21258 0.17840
  Recv: 105.00 2.72 1.33381 0.53773 0.45297 0.49032 0.19767 0.16651
  Recv: 106.00 2.77 1.21448 0.44152 0.47061 0.43806 0.15926 0.16975
  Recv: 107.00 2.54 1.08040 0.36589 0.44023 0.42495 0.14391 0.17315
  Recv: 108.00 2.59 1.05615 0.32241 0.47006 0.40775 0.12448 0.18148
  Recv: 109.00 2.64 1.15173 0.29849 0.58971 0.43653 0.11313 0.22351
  Recv: 110.00 2.69 1.33526 0.30321 0.71248 0.49693 0.11284 0.26516
  Recv: 111.00 2.74 1.61857 0.35240 0.81952 0.59157 0.12880 0.29952
  Recv: 112.00 2.79 1.94898 0.37601 0.87473 0.69966 0.13498 0.31402
  Recv: 113.00 2.52 1.68980 0.23453 0.71156 0.67042 0.09305 0.28231
  Recv: 114.00 2.57 1.69792 0.16240 0.66092 0.66188 0.06330 0.25764
  Recv: 115.00 2.61 1.65134 0.14995 0.58935 0.63257 0.05744 0.22576
  Recv: 116.00 2.66 1.59241 0.16158 0.50917 0.59953 0.06084 0.19170
  Recv: 117.00 2.70 1.39377 0.13758 0.41791 0.51581 0.05091 0.15466
  Recv: 118.00 2.75 1.51073 0.16867 0.45188 0.54966 0.06137 0.16441
  Recv: 119.00 2.80 1.45295 0.18468 0.41473 0.51979 0.06607 0.14837
  Recv: 120.00 2.84 1.28860 0.17773 0.38762 0.45334 0.06253 0.13637
  Recv: 121.00 2.53 1.21289 0.16201 0.37601 0.47964 0.06407 0.14869
  Recv: 122.00 2.57 1.17970 0.15645 0.35765 0.45890 0.06086 0.13912
  Recv: 123.00 2.61 1.12521 0.16072 0.37712 0.43061 0.06151 0.14432
  Recv: 124.00 2.66 1.10012 0.16166 0.37640 0.41425 0.06087 0.14173
  Recv: 125.00 2.70 1.07538 0.15410 0.37874 0.39848 0.05710 0.14034
  Recv: 126.00 2.74 0.95284 0.13575 0.31709 0.34749 0.04951 0.11564
  Recv: 127.00 2.79 0.91048 0.11894 0.33758 0.32683 0.04270 0.12118
  Recv: 128.00 2.83 1.04024 0.14154 0.38455 0.36760 0.05002 0.13589
  Recv: 129.00 2.87 0.86949 0.15356 0.33961 0.30252 0.05343 0.11816
  Recv: 130.00 2.50 0.76300 0.18403 0.30578 0.30496 0.07355 0.12222
  Recv: 131.00 2.54 0.68856 0.25087 0.29105 0.27102 0.09875 0.11456
  Recv: 132.00 2.58 0.67250 0.34308 0.31102 0.26071 0.13300 0.12057
  Recv: 133.00 2.62 0.60733 0.41113 0.26756 0.23192 0.15699 0.10217
  Recv: 134.00 2.66 0.62634 0.46760 0.27514 0.23562 0.17590 0.10350
  Recv: 135.00 2.70 0.66844 0.49100 0.27874 0.24775 0.18198 0.10331
  Recv: 136.00 2.74 0.79570 0.51940 0.28896 0.29059 0.18969 0.10553
  Recv: 137.00 2.78 0.87707 0.48945 0.31941 0.31565 0.17615 0.11495
  Recv: 138.00 2.82 0.83658 0.42914 0.30674 0.29673 0.15221 0.10880
  Recv: 139.00 2.86 0.88278 0.40416 0.34734 0.30863 0.14130 0.12143
  Recv: 140.00 2.90 0.83519 0.35901 0.32898 0.28783 0.12373 0.11338
  Recv: 141.00 2.94 0.84354 0.34291 0.37297 0.28660 0.11651 0.12672
  Recv: 142.00 2.99 0.81420 0.31243 0.33999 0.27275 0.10466 0.11389
  Recv: 143.00 2.52 0.65446 0.23634 0.30451 0.25942 0.09368 0.12070
  Recv: 144.00 2.56 0.63765 0.22276 0.29454 0.24926 0.08707 0.11513
  Recv: 145.00 2.59 0.62128 0.20212 0.28252 0.23952 0.07792 0.10892
  Recv: 146.00 2.63 0.55110 0.17456 0.25640 0.20956 0.06638 0.09750
  Recv: 147.00 2.67 0.60478 0.19506 0.26290 0.22686 0.07317 0.09861
  Recv: 148.00 2.70 0.48269 0.15615 0.20274 0.17862 0.05779 0.07503
  Recv: 149.00 2.74 0.52254 0.16864 0.22939 0.19078 0.06157 0.08375
  Recv: 150.00 2.78 0.55978 0.17925 0.26769 0.20166 0.06458 0.09644
  Recv: Maximum resonant gain: 3.99 at frequency: 79.00
  Recv: ZV shaper selected
  Recv: Frequency: 79.00 damping ratio: 0.16014
  ```
</details>
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

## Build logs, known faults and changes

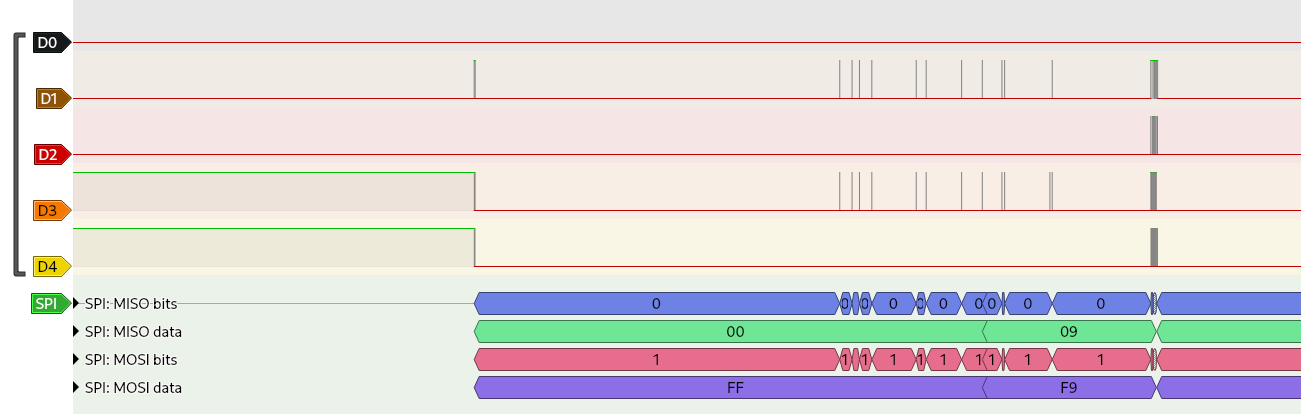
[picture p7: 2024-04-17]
Signal Captures/1_IdleStateToCommandIssue_2MHz.png

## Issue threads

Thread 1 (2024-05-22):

MK3.5 xbuddy 0.3.7 success report (with workaround)

m-kozlowski, 2024-05-22:
PA10 (accelCS) pin is used in MK3.5 firmware as print fan tacho in, so I initially thought that the lack of communication was simply due to the CS pin not being mapped. However, it turned out that the MK3.5 has special handling in the PrusaAccelerometer constructor. Connecting the logic analyzer to the cables, still without the accelerometer connected, I observed the correct pin state change after issuing gcode M959.
Unfortunately, after connecting the accelerometer (Adafruit), the CS remained high all the time, as if xbuddy could not sink enough current to drive pin low. Perhaps version 0.3.7 includes some change to handle the fan signal on this pin? I didn't bother to disassemble the board to check this, instead I "helped" the pin reach a low state by soldering a 2K2 resistor in the accelerometer between GND and CS.
After this modification, the M959 works flawlessly.

JuanPuchol, 2024-05-23:
Thank you very much for your solution, I have been testing the same (high) value on CS pin but I didn't know where to put the resistor (and what value) exactly

MCDELTAT, 2024-05-25:
@m-kozlowski Thanks for your feedback, extremely helpful as I have a 0.2.7 board. I've added the resistor to my PCB design which I'll be uploading shortly.

thedave42, 2024-05-25:
Has anyone else had success with the 0.3.7 board by adding the 2K2 resistor? I have the MK4 upgrade and it came with the 0.3.7 board.  I just tried this out, but issuing the M959 command causes the printer to crash.

I'm using the Adafruit Accelerometer.

<details>
<summary>Checked the soldering and the pin connections a couple of times with a multimeter.</summary>

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
</details>

But I don't have an LA to do any additional analysis...

JuanPuchol, 2024-05-26:
Hello,

M959 is working on my Enhanced MK4. I have done a divider circuit (you need two equal resistors serial soldier, in my case two 1K resistors) one end goes to GND the other end goes to CS cable pin, and the resistors join goes to CS Adafruit pin). In this way you send 1.53v instead 3.3v. Please try it!
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

m-kozlowski, 2024-05-26:
Or maybe simply get rid of R8 and replace D2 with a jumper?
Haven't tried it yet, but if I'm guessing right, CS is currently pulled up
on both ends.

https://learn.adafruit.com/assets/28587

niedz., 26 maj 2024 o 08:50 JuanPuchol ***@***.***>
napisał(a):

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

thedave42, 2024-05-26:
> I have done a divider circuit (you need two equal resistors serial soldier, in my case two 1K resistors) one end goes to GND the other end goes to CS cable pin, and the resistors join goes to CS Adafruit pin). In this way you send 1.53v instead 3.3v. Please try it!

@JuanPuchol this worked!  Thank you very much!

jimwsmith, 2024-06-10:
> Hello,
>
> M959 is working on my Enhanced MK4 (xBuddy 0.3.7). I have done a divider circuit (you need two equal resistors serial solder, in my case two 1K resistors) one end goes to GND the other end goes to CS cable pin, and the resistors join goes to CS Adafruit pin). In this way you send 1.53v instead 3.3v. Please try it! ![Divider circuit](https://private-user-images.githubusercontent.com/47700064/333853274-e2756e03-e225-4bbd-9cbc-67527a5ffe3c.jpg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)

This worked for me too (simple 2K resistor didn't work)

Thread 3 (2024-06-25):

PCB v0.2 (and possibly v0.1) README lists incorrect Accelerometer chip

welnanick, 2024-06-25:
The PCB v0.2 Readme lists LIS2DHTR as the part number, but the schematic for the PCB uses LIS2DH12TR. LIS2DHTR is not compatible with the PCB design/schematic.

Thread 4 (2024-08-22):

Tried LIS2DH12TR from amazon and got accelerometer communication error

nuclearmistake, 2024-08-22:
Followed instructions exactly, checked and rechecked wiring repeatedly, but still not able to communicate with accelerometer on stock MK4.

I also tried the voltage divider on the CS pin that some people used with the sparkfun accelerometer, but it didn't make a difference.

Could you number the color coded pins in your images? And share some assembled photos?

MCDELTAT, 2024-08-22:
What model xBuddy board do you have? I've only personally tested it on a 0.2.7 revision main board. The voltage divider thing has some positive comments from people, but can't personally confirm.

As for numbering the images. I guess I could, it'd essentially still create the same problem. You need to know the correct orientation on the printer side. Pin 6 is the upper pin when plugged into the board. Then the colors just go from there.

As a related note, this project is likely resolved and closed. Prusa has released an official accelerometer kit for the MK4S, MK3.9S, and MK3.5S that can be found here: https://www.prusa3d.com/product/accelerometer-set/

While that list obviously doesn't include the MK4, I see no reason why it wouldn't, as it is likely the same exact chip we're using in our boards here. I have one pre-ordered, along with the MK4S upgrade kit. So I won't know until ~Sep 10th. If it works on my MK4 pre-upgrade, then I'll be archiving this repo. Looks like they already did a good job at designing mounts, etc.

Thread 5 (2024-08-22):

Prusa XL accelerometer ground truth

nuclearmistake, 2024-08-22:
The XL has an accelerometer, right? Couldn't that be used as a baseline to determine wiring and modifications needed for off-the-shelf accelerometer dev boards?

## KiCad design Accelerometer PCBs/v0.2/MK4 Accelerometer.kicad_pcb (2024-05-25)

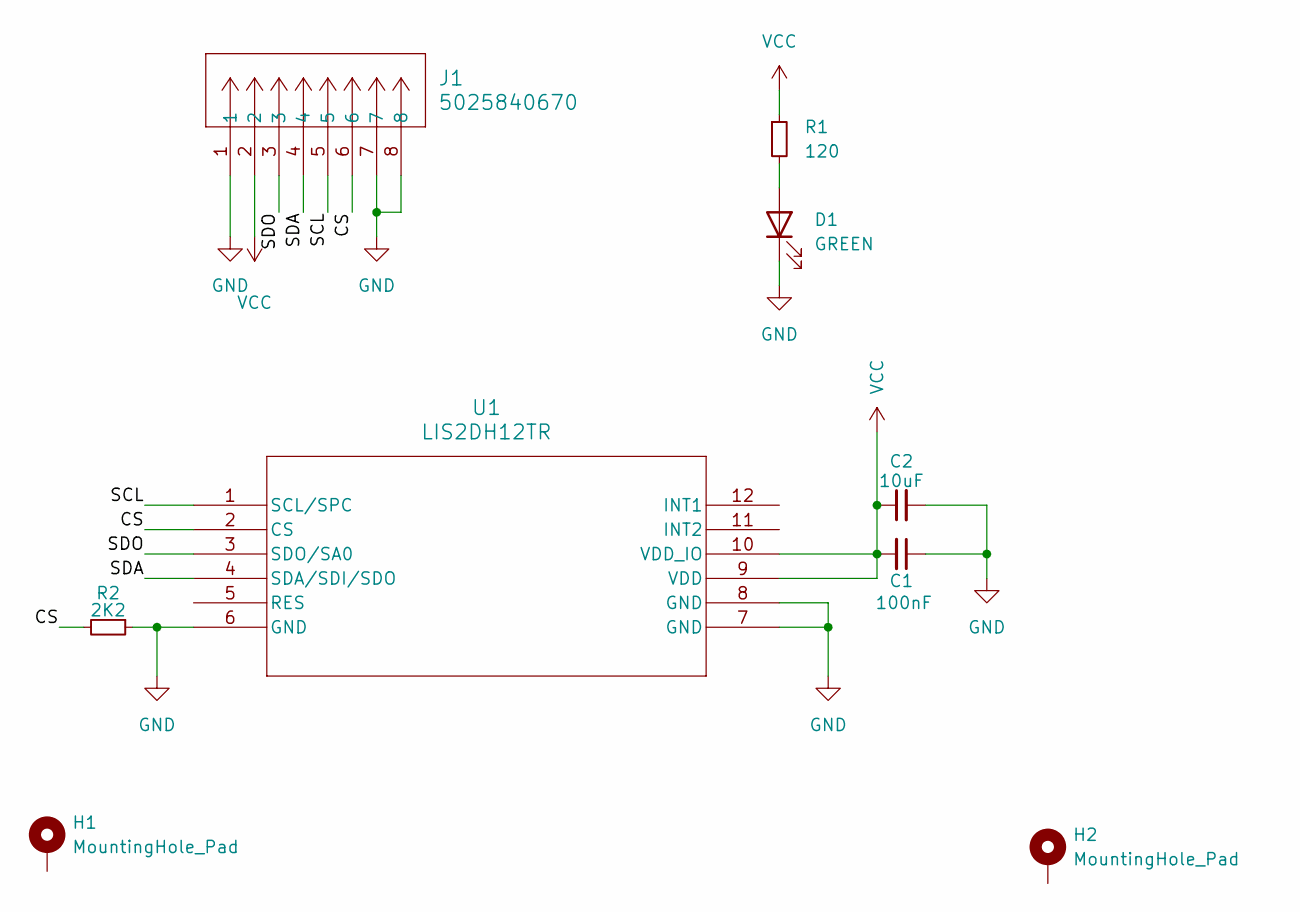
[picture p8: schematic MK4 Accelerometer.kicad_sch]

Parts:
C1: 100nF; C_0603_1608Metric
C2: 10uF; C_0603_1608Metric
D1: GREEN; LED_0603_1608Metric
H1, H2: MountingHole_Pad; MountingHole_2.2mm_M2_Pad
J1: 5025840670; CON_5025840670_MOL
R1: 120; R_0603_1608Metric
R2: 2K2; R_0603_1608Metric
U1: LIS2DH12TR; LGA-12_STM

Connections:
/CS: J1.6, R2.2, U1.2 (CS)
/SCL: J1.5, U1.1 (SCL/SPC)
/SDA: J1.4, U1.4 (SDA/SDI/SDO)
/SDO: J1.3, U1.3 (SDO/SA0)
GND: C1.1, C2.2, D1.1 (K), J1.1, J1.7, J1.8, R2.1, U1.6 (GND), U1.7 (GND), U1.8 (GND)
unnamed: D1.2 (A), R1.2
VCC: C1.2, C2.1, J1.2, R1.1, U1.9 (VDD), U1.10 (VDD_IO)

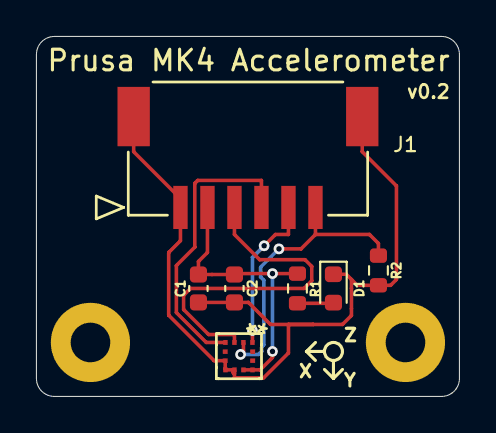
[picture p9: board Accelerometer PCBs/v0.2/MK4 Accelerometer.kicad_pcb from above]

Board: 2 copper layers, 23.5 x 20.0 mm, 9 parts (0 on the bottom side), 7 nets.

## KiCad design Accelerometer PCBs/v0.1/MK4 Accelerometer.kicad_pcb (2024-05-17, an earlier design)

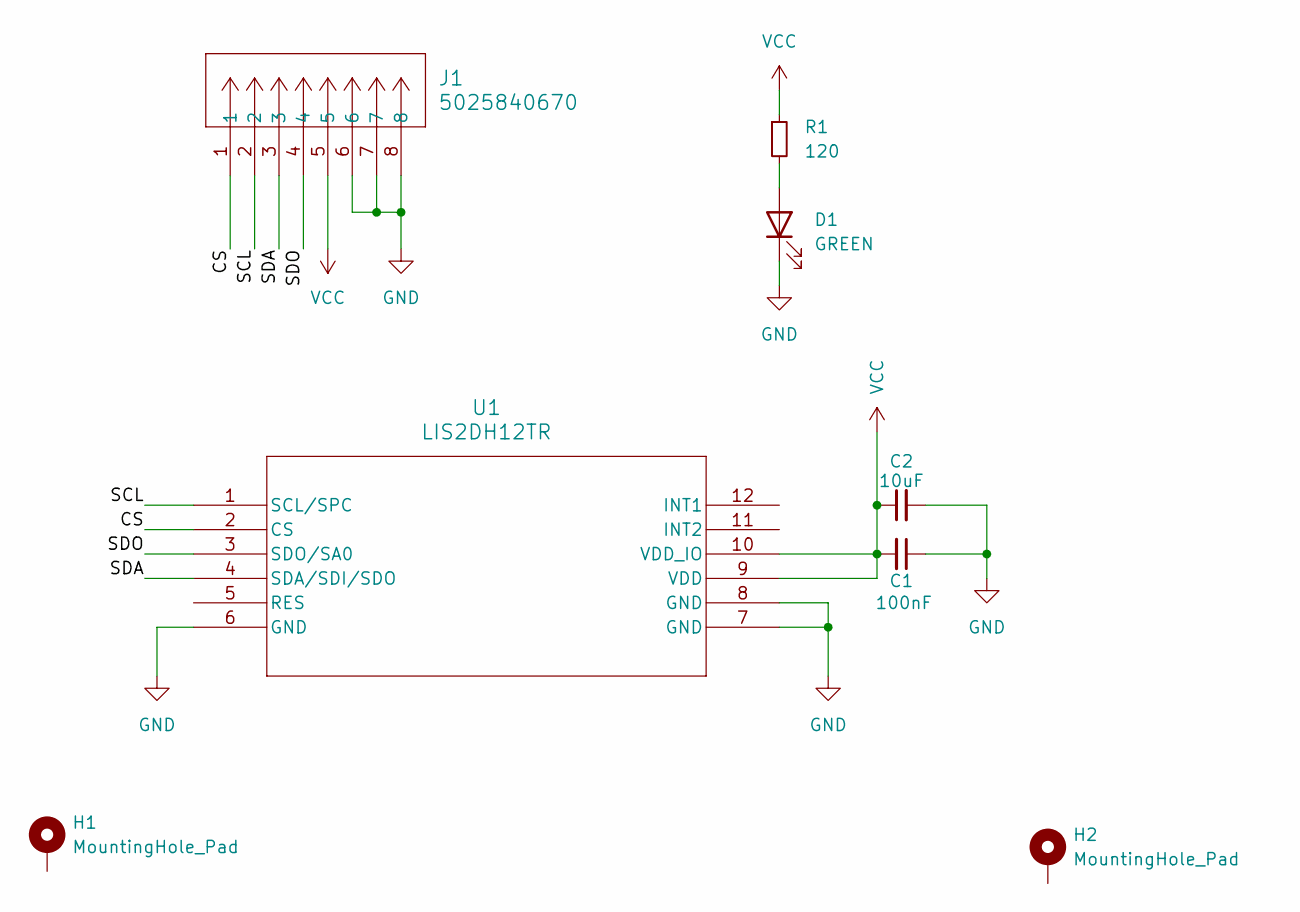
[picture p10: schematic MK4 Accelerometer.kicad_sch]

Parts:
C1: 100nF; C_0603_1608Metric
C2: 10uF; C_0603_1608Metric
D1: GREEN; LED_0603_1608Metric
H1, H2: MountingHole_Pad; MountingHole_2.2mm_M2_Pad
J1: 5025840670; CON_5025840670_MOL
R1: 120; R_0603_1608Metric
U1: LIS2DH12TR; LGA-12_STM

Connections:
/CS: J1.1, U1.2 (CS)
/SCL: J1.2, U1.1 (SCL/SPC)
/SDA: J1.3, U1.4 (SDA/SDI/SDO)
/SDO: J1.4, U1.3 (SDO/SA0)
GND: C1.1, C2.2, D1.1 (K), J1.6, J1.7, J1.8, U1.6 (GND), U1.7 (GND), U1.8 (GND)
unnamed: D1.2 (A), R1.2
VCC: C1.2, C2.1, J1.5, R1.1, U1.9 (VDD), U1.10 (VDD_IO)

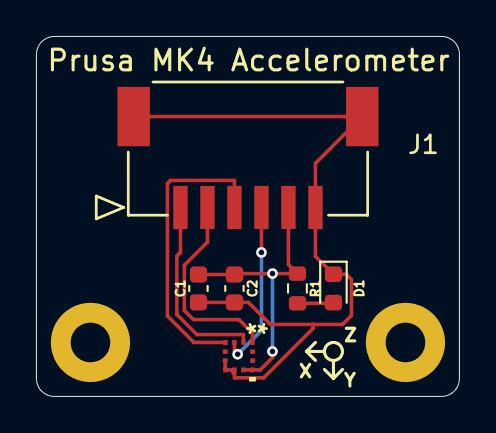
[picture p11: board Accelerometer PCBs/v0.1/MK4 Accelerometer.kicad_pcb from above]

Board: 2 copper layers, 23.5 x 20.0 mm, 8 parts (0 on the bottom side), 7 nets.

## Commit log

2024-04-15 Update cable link, add tests in Klipper mode
2024-04-15 Link to the 3D printed mounts
2024-04-18 Document Adafruit LIS3DH board as working
2024-05-17 Added v0.1 of PCB
    [MK4 Accelerometer.kicad_pcb, MK4 Accelerometer.kicad_sch, MK4 Accelerometer.step]
2024-05-25 0.2 PCB
    [MK4 Accelerometer.kicad_pcb, MK4 Accelerometer.kicad_sch]
